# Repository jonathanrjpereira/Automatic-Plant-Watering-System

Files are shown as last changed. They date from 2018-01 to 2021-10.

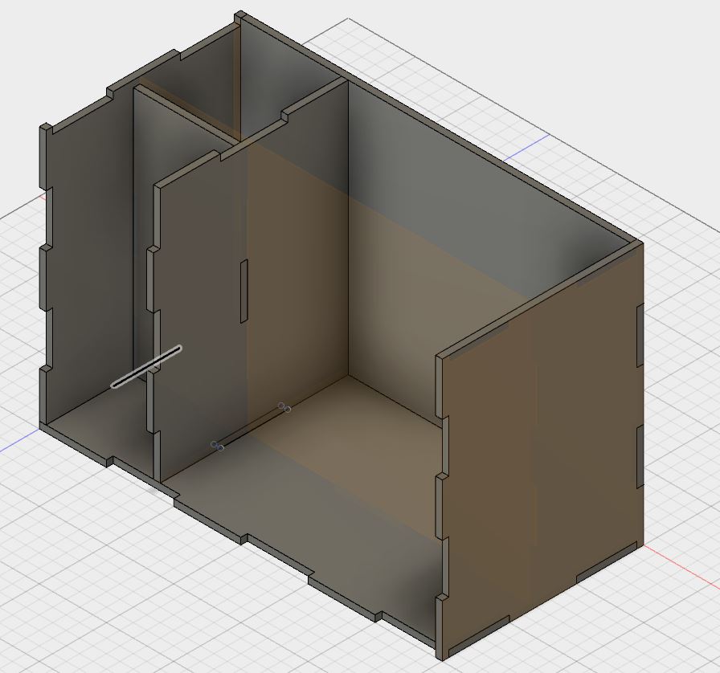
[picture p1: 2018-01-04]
Mechanical Design/Views/Isometric2.JPG

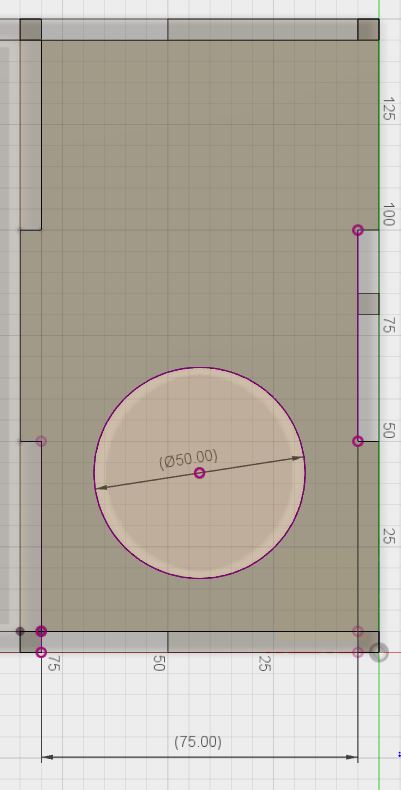
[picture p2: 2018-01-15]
Mechanical Design/Views/Bottle Dimensions.JPG

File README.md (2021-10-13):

# Automatic Plant Watering System using Arduino
Meet Sprouter - the Modern Indoor Planter which automatically waters your plants, herbs, vegetables, etc and will revolutionize your gardening game.

**Full Video:**
Sprout: Arduino Automatic Self Watering Planter (https://youtu.be/lRu-Z6gGrvc)

It consists of an integrated water reservoir from which water is pumped & keeps the plant's soil hydrated.

A soil moisture sensor is calibrated such that it periodically measures the moisture of the soil thereby regulating the water flow. If the soil is too dry, the water pump automatically switches ON and goes OFF when the soil moisture has reached the desired level.

If you're the person who underwaters their plants, Sprouter will ensure you will never have to worry about being a bad gardener again. And if you're the sort of person who overwaters their plants to compensate for absenteeism, it means your not in danger of drowning your plants or seeds.

Sprouter's water reservoir capacity is around 500 ml / 17 fl oz, which allows you to neglect your plants for as long as a month before it needs a refill.



The optional Bluetooth feature can be used to manually toggle & control the water pump wirelessly from your smartphone.

## Electronic Design


**Electronic Components List:-**  
Arduino Nano:  [AliExpress](http://s.click.aliexpress.com/e/bkvVYL0k)  
DC Water Pump:  [AliExpress  
](http://s.click.aliexpress.com/e/bfNLbZuy)Soil Moisture Sensor:  [AliExpress  
](http://s.click.aliexpress.com/e/87kineY)HC-05 Bluetooth Module:  [AliExpress  
](http://s.click.aliexpress.com/e/CZ6XTMk)LM7805 Voltage Regulator:  [AliExpress](http://s.click.aliexpress.com/e/bEYiDSbm)[  
](https://lcsc.com/?s_url=nTajLG)IRF540 MOSFET:  [AliExpress](http://s.click.aliexpress.com/e/cB3xxOSy)  
[](http://s.click.aliexpress.com/e/cB3xxOSy)220 Ohm Resistor:  [AliExpress](http://s.click.aliexpress.com/e/9vWhcpa)  
[](http://s.click.aliexpress.com/e/9vWhcpa)IN4001 Diode:  [AliExpress](http://s.click.aliexpress.com/e/cbX7VpXE)  
[](http://s.click.aliexpress.com/e/cbX7VpXE)Header Pin Strips:  [AliExpress](http://s.click.aliexpress.com/e/cmO4dYcu)  
[](http://s.click.aliexpress.com/e/cmO4dYcu)DC Barrel Jack:  [AliExpress](http://s.click.aliexpress.com/e/EFO7b4M)  
[](http://s.click.aliexpress.com/e/EFO7b4M)Screw Terminal Block:  [AliExpress](http://s.click.aliexpress.com/e/RWeMW4u)  
[](http://s.click.aliexpress.com/e/RWeMW4u)PCB:  [AliExpress  
](http://s.click.aliexpress.com/e/b3XHCl9O)[](http://s.click.aliexpress.com/e/b3XHCl9O)AC-12VDC Adapter:  [AliExpress](http://s.click.aliexpress.com/e/bWW0wsRq)

**Tools:-**  
Soldering Iron:  [AliExpress  
](http://s.click.aliexpress.com/e/bC7ng4wy)Solder Wire:  [AliExpress](http://s.click.aliexpress.com/e/uoYCrrw)

**Power Block**: The 7805 regulates the supply voltage and reduces it to a constant 5V making it suitable to run the Arduino & Soil Moisture Sensor.

**Pump Control**: The MOSFET acts as a switch which is controlled by the Arduino. We use the MOSFET since the Arduino cannot directly power the DC Pump. The resistor connected to the gate of the MOSFET prevents the MOSFET from getting damaged. The flyback diode connected across the pump provides a path for dissipation of stored energy when the pump is switched off. The  _Anode_  of the Diode is connected to the  _Drain_  of the MOSFET. The  _Cathode_  of the Diode is connected to the  _9V_  supply rail. The  _Source_  of the Diode is connected to  _GND_.

**Moisture Sensor**: The sensor feeds an analog value to the Arduino. The threshold level of moisture is calibrated by the user depending on the type of plant used.

**Bluetooth Module**: Uses Serial Communication to transfer data between the Arduino and your Smartphone.



## Electronic Assembly
Electronic Assembly
A 1x Scale printable PCB as well as the board view and schematic is available in the GitHub repository.

[Sprouter: GitHub/Electronics](https://github.com/jonathanrjpereira/Automatic-Plant-Watering-System-using-Arduino/tree/master/Electronics)

The repository also contains an A4 size PDF which contains multiple PCB's on a single page. This can be used to make multiple PCB's at a time for mass production

## Software & Bluetooth Configuration
**Software**: The Moisture Sensor is connected to an Analog Input pin of the Arduino. A threshold value determines whether the Pump should be ON/OFF.
You can find the code at  [Sprouter: GitHub/Code](https://github.com/jonathanrjpereira/Automatic-Plant-Watering-System-using-Arduino/blob/master/Code/plant/plant.ino)
Feel free to modify & contribute to the GitHub repository.

**Smartphone App & Bluetooth Configuration**: The HC-05 Bluetooth module is the intermediate block between the Smartphone & Arduino. It uses Serial Communication to send data from the Smartphone to the Arduino & acts as a Remote Control.
The app transmits the value '48' or '49' which represent 'ON' & 'OFF' respectively. The pump can hence be controlled wirelessly.



Simply open the app, scan for discoverable devices & pair with the HC-05 module. then click on 'Switch Mode' and toggle the onscreen button.
The app is available at  [Bluetooth App](https://play.google.com/store/apps/details?id=com.giumig.apps.bluetoothserialmonitor&hl=en)

## Mechanical Design


The main body of Sprouter is a 30cm X 15cm X 19cm Box made out of MDF.

All Mechanical Design steps have been clearly demonstrated in the video attached at the start of the Instructable. You can also check it out at  [Sprout: Video/Mechanical Design](https://www.youtube.com/watch?v=lRu-Z6gGrvc&index=2&list=LLKJ2W0HPvFnYySV5TITcHsg&t=47s)


The box is divided into two sections:

1.  The larger section contains the Soil & Plants
2.  The smaller section is further divided into two more sections such that one section contains the Circuit Board while the other contains the Water Reservoir.

The water reservoir is a 500ml plastic bottle.



The MDF box has 8 separate interlocking faces which can be laser cut and slotted into each other.

The Laser Cutting files, Fusion 360 Design file (3D Design file), isometric as well as orthogonal views of each face can be found at  [Sprout: GitHub/Mechanical Design](https://github.com/jonathanrjpereira/Automatic-Plant-Watering-System-using-Arduino/tree/master/Mechanical%20Design)

You can also find editable Illustrator files in the GitHub repository which can be modified to your specific requirements/dimensions and then can be laser cut.
## Mechanical Assembly: Bottle Preparation



The water reservoir is a 500ml plastic bottle. A typical 500ml plastic Soda bottle can be used for this.

The maximum diameter of the bottle should be 74mm. The maximum diameter of the cap of the bottle should be 50mm. The maximum height from the base of the bottle to the lowest part of the cap should be 18.5 cm.

The bottle must be cut about 50mm above its base so that the pump can be placed within it. Holes must be cut into the bottle such that the Outlet Pipe and Power wires can be fed through the bottle.


Once the Outlet Pipe and wires have been taken out through their respective holes, the bottle can be sealed again. To seal the bottle we must use an Epoxy Compound which will harden within a few hours. This will prevent any water from leaking out.

The water can be refilled from the top of the bottle by simply opening its cap.

## Mechanical Assembly: Box Preparation
Once you have successfully laser cut the 8 different faces of the box, Apply several coats of a high-quality wood varnish to each side of each face.This makes it highly water repellant & makes it resistant to moisture & humidity.

Mount the Power Jack on the Back Plate too & connect it to the Circuit Board.



Mount the Circuit Board on the Back Plate of the Box such that it fits within their respective section.

Pull the Pump Outlet Pipe through the given holes such that it reaches the Plant soil section. Do the same for the Moisture Sensor wires.

Don't forget to connect the Water Pump to the Circuit Board as shown in the Schematic

Begin interlocking the different faces of the Box and ensure that bottle fits snuggly into its designated area.

Apply wood glue or an adhesive to seal the entire box.

## Mechanical Assembly: Cement Finish
Mechanical Assembly: Cement




This step will determine the out texture & final finish of the box as well as give the planter another protective coating.

Apply glue to each face of the box. Then sprinkle some cement over the glue. Use the remaining circular MDF piece which was cut from the Top Plate to smoothen the cement across the surface of each face of the box. Repeat this step for each face of the box as demonstrated in the video.

Once the cement dries, sprinkle with water every 6 hours for 1 day. This will allow the cement to cure, with no cracks and will also prevent water from leaking.

## Add the Soil & Plants



Once the cement has cured, fill the box with soil.

Remember to heat seal the end of the Outlet pipe before making a hole in it for the dripper. The dripper is used to regulate the water coming out of the pipe so that the water does not flow out of the planter.

Place the Soil Moisture Sensor inside the soil.

Power Sprouter through the Power Jack at the Back Plate & make sure fill the water reservoir to the full level.

Test whether everything works and you should be done.

## Contributing
Are you a programmer, engineer or designer who has a great idea for a new feature/design in Sprouter? Maybe you're just a beginner or you've spotted a bug? Feel free to grab our code, schematics, 3D design files & laser cutting files from Github and tinker with it.

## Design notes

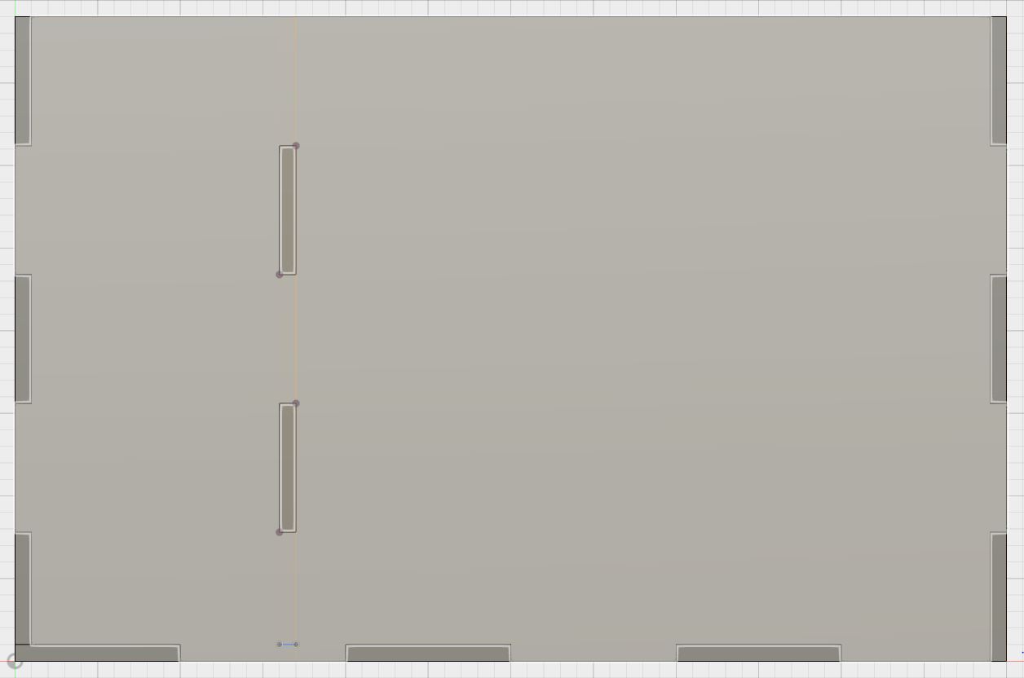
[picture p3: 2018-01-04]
Mechanical Design/Views/Front.JPG

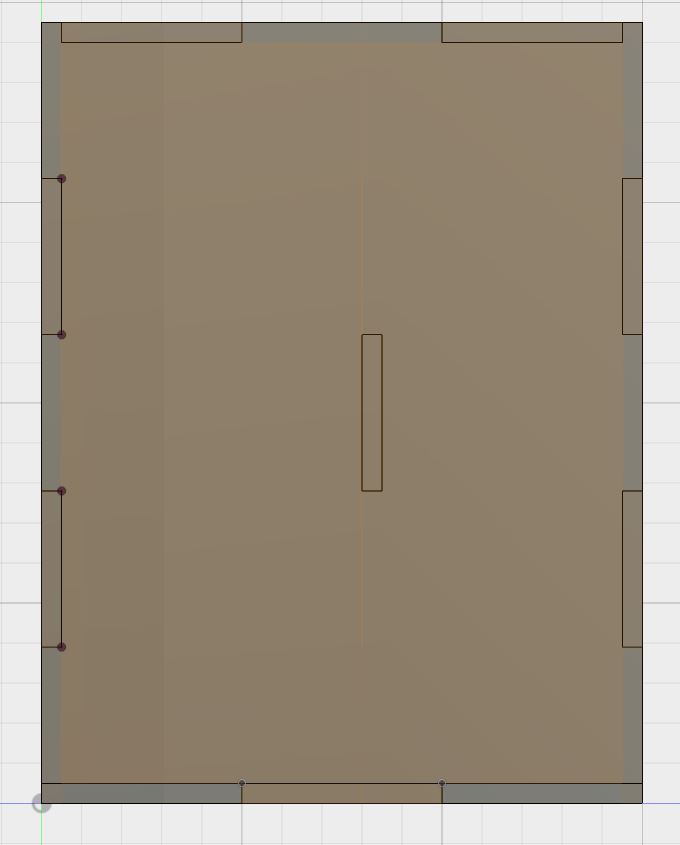
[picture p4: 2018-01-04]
Mechanical Design/Views/Left.JPG

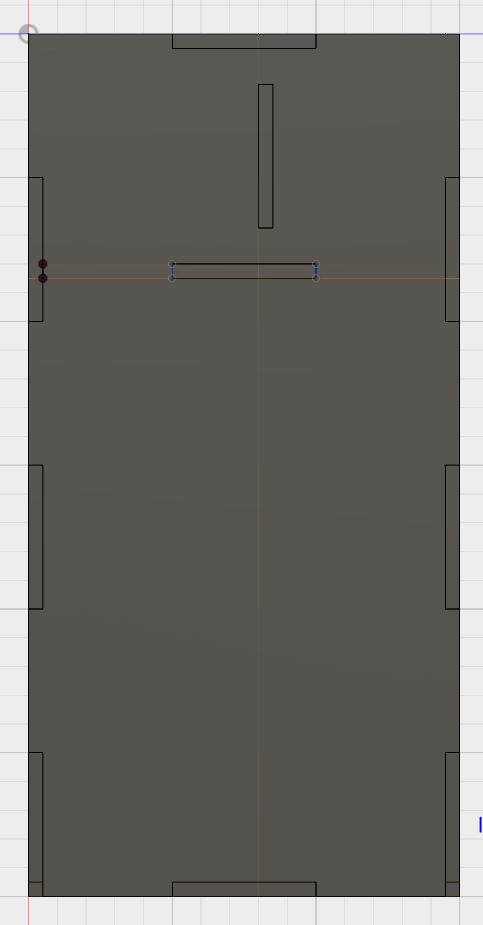
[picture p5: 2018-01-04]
Mechanical Design/Views/Base.JPG

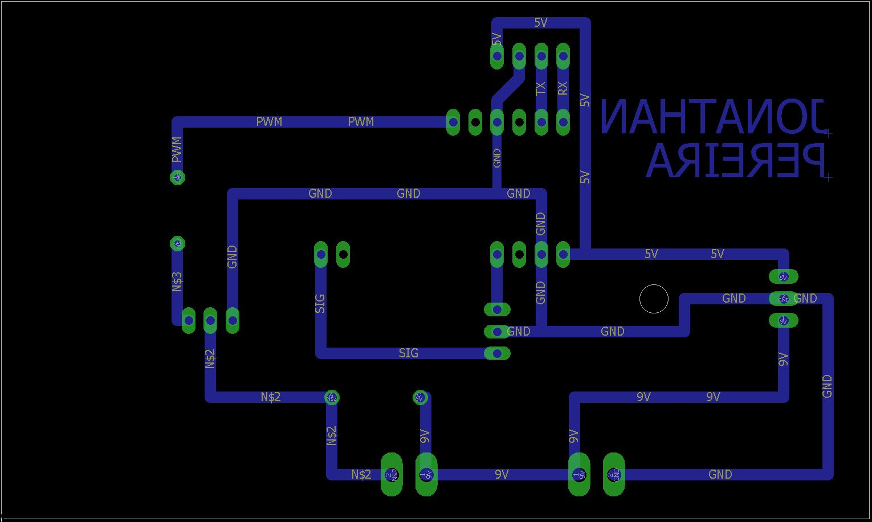
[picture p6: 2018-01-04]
Electronics/Board.JPG

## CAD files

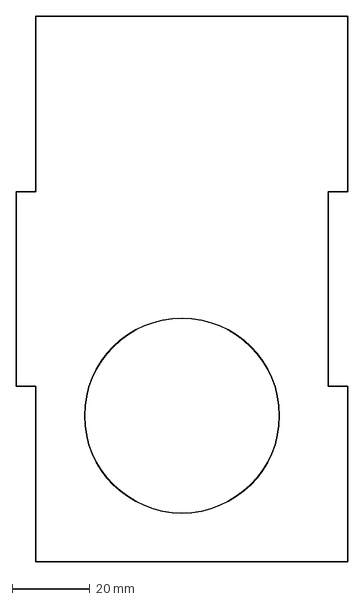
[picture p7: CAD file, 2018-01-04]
Mechanical Design/Laser Cutting/Top.dxf
85.0 x 140.0 mm

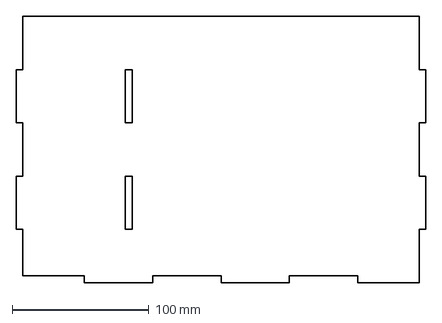
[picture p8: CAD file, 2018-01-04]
Mechanical Design/Laser Cutting/Front.dxf
300.0 x 195.0 mm

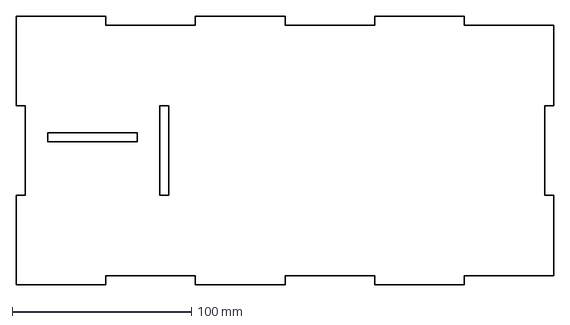
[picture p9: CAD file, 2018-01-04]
Mechanical Design/Laser Cutting/Base.dxf
300.0 x 150.0 mm

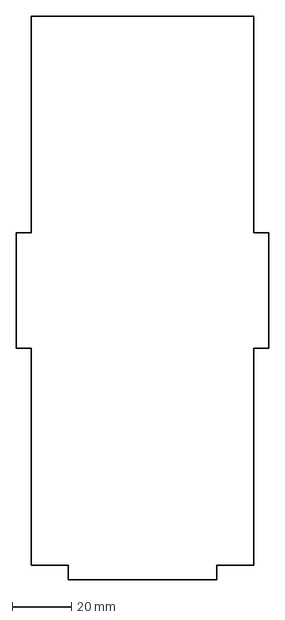
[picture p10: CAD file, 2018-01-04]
Mechanical Design/Laser Cutting/Div4.dxf
85.0 x 190.0 mm

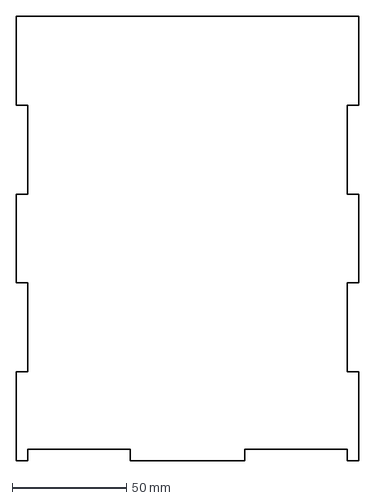
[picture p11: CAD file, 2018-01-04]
Mechanical Design/Laser Cutting/Right.dxf
150.0 x 195.0 mm

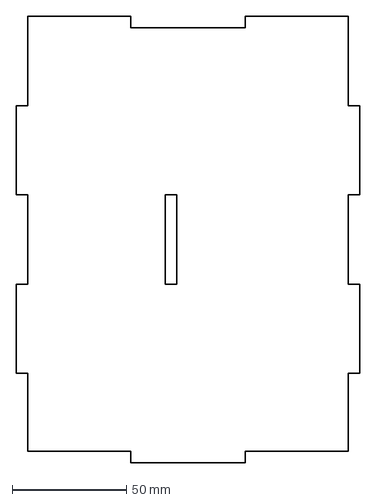
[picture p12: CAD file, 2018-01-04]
Mechanical Design/Laser Cutting/Div2.dxf
150.0 x 195.0 mm

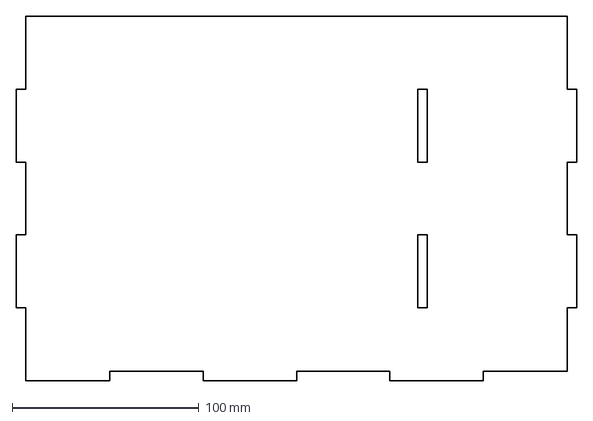
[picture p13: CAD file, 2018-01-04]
Mechanical Design/Laser Cutting/Back.dxf
300.0 x 195.0 mm

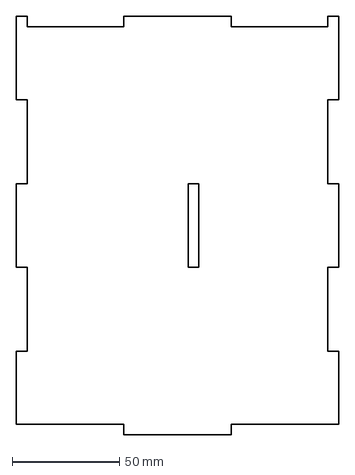
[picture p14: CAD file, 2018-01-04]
Mechanical Design/Laser Cutting/Left.dxf
150.0 x 195.0 mm

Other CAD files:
Mechanical Design/plant.f3d

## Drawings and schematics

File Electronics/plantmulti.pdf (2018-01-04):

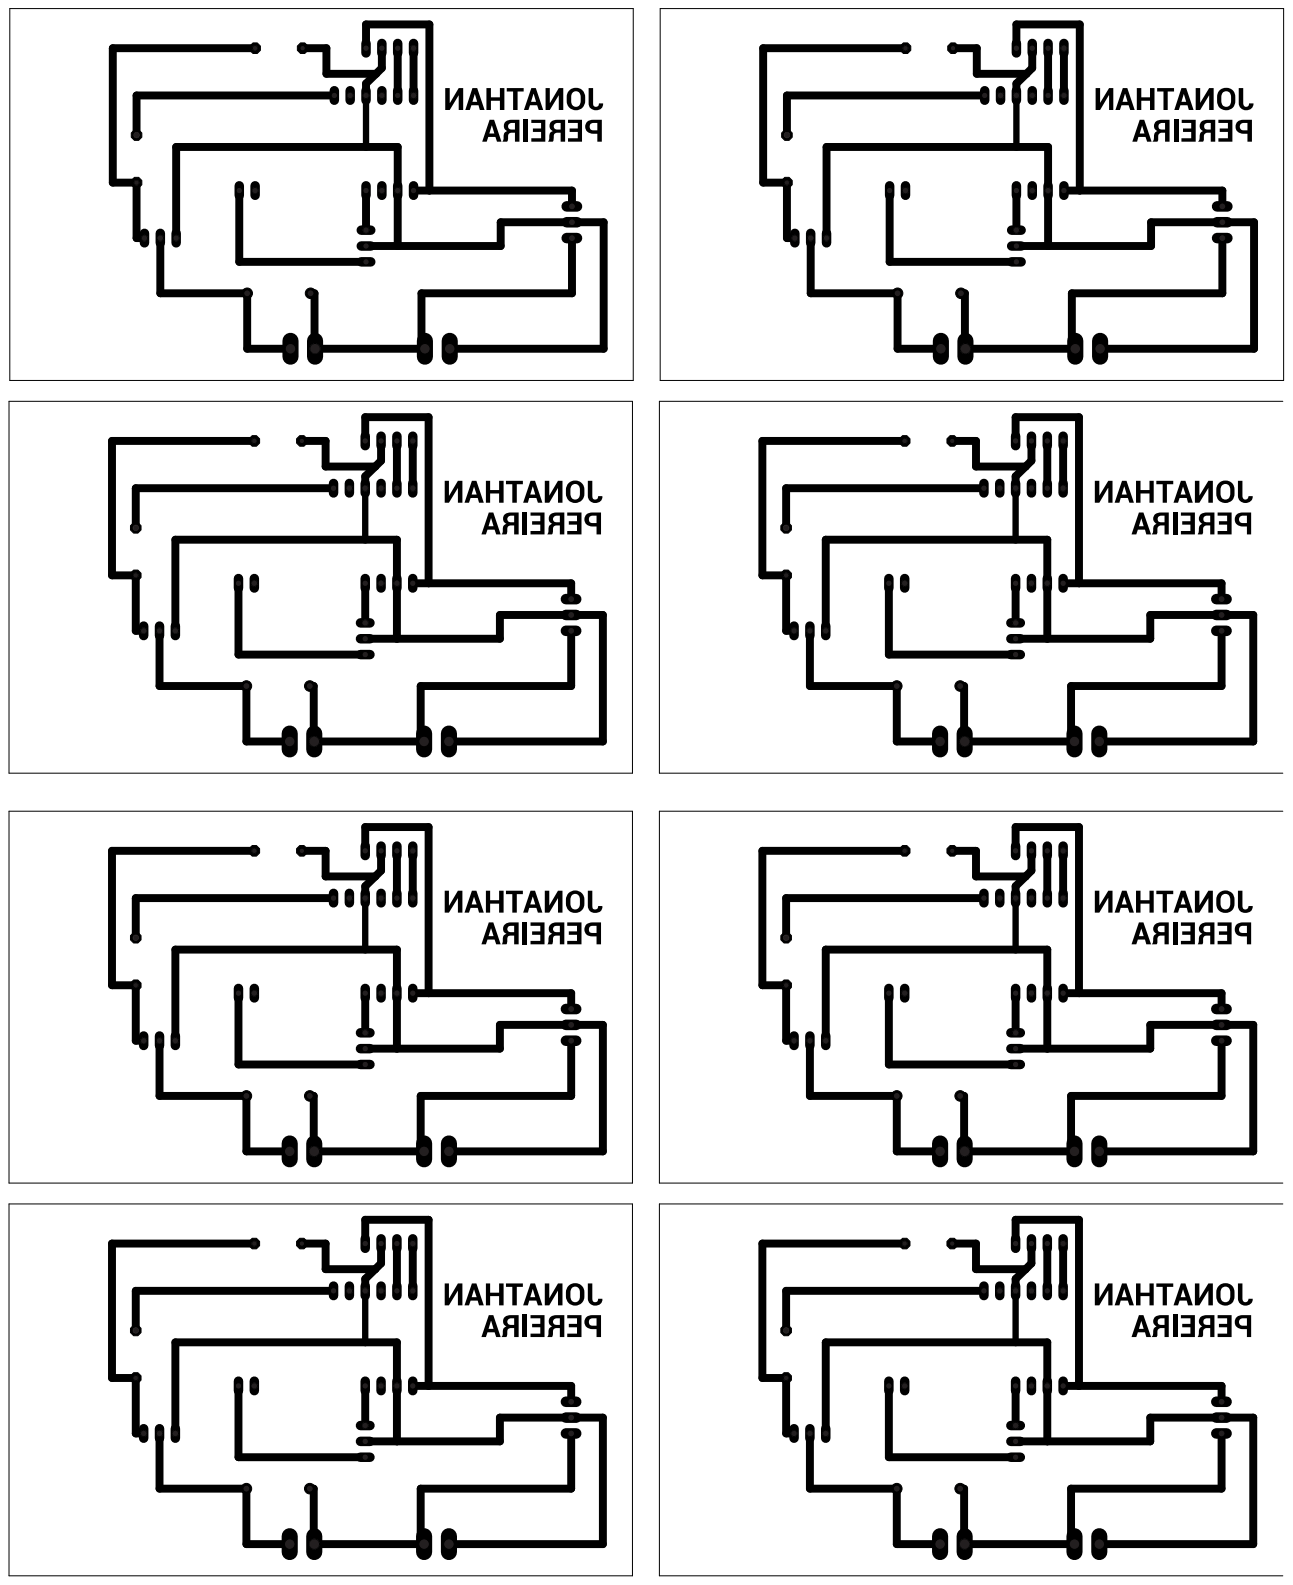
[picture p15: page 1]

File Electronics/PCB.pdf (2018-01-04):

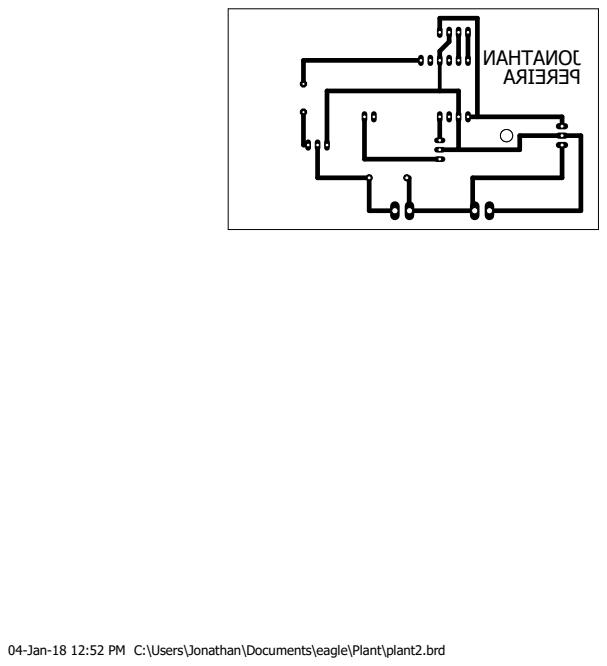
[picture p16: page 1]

04-Jan-18 12:52 PM C:\Users\Jonathan\Documents\eagle\Plant\plant2.brd

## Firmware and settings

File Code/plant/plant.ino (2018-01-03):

int blue = 0;  // for incoming serial data
int moisture_sensor  = A0;
int moisture;
int limit = 500;
int pump = 3;
int led = 13;
int pump_time = 3000;
void setup()
{
  Serial.begin(9600); // opens serial port, sets data rate to 9600 bps
  pinMode(moisture_sensor,INPUT);
  pinMode(pump,OUTPUT);
  pinMode(led,OUTPUT);
}

void loop() 
{
  moisture = analogRead(moisture_sensor);
  Serial.print("Moisture=");
  Serial.print(moisture);
  Serial.println();
  
  while(Bluetooth()==1)
  {
    Pump(1);
    blue = 0;
    break;
  }
  while(Bluetooth()==0)
  {
    if(moisture<limit)
    {
      Pump(1);
      break;  
    }
    else
    { 
      Pump(0);
      break;
    }
  }
}

int Bluetooth()
{
   // send data only when you receive data:
   if(Serial.available() > 0) 
   {
    // read the incoming byte:
    blue = Serial.read();

    // say what you got:
    Serial.print("Bluetooth");
    Serial.println(blue);
    if(blue == 48)
      return 0;
    if(blue == 49)
      return 1;
  }
  else 
  return 0;
}

void Pump(int stat)
{
  if(stat == 0)
  {
    digitalWrite(pump,stat);
    digitalWrite(led,stat);
    Serial.println("Pump OFF");
  }
  if(stat == 1)
  {
    digitalWrite(pump,stat);
    digitalWrite(led,stat);
    Serial.println("Pump ON");
    delay(pump_time);
  }
}

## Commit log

2018-01-04 Electronics
    Schematic, Board, PCB.
    Eagle Files are hosted on Instructable since due to GitHub Language detection error.
2018-01-04 Multiple PCB
    To Scale A4 size Muliple PCB printable using Iron-Laser Printer PCB Method
2018-01-04 3D Fusion 360
    3D Design File.
    Autodesk Fusion 360
    [plant.f3d]
2018-01-04 Laser Cutting
    PDFs for Laser Cutting for all views.
    Editable Adobe Illustrator files for all views.
    [Back.dxf, Base.dxf, Div2.dxf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]
2018-01-15 Orthogonal View
    Top Plate - Bottle Dimensions
